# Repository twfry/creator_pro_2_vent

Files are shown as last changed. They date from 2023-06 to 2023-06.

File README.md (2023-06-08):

# Creator Pro 2 Vent Attachment for Hood

## Description

An adapter to easily attach a vent hose to the back of the Creator Pro 2's existing hood and fully vent all fumes. Does not require modifying the hood or the Creator Pro 2 in any manner.

Designed in OpenSCAD and uses the Round Anything library to design it entirely with smooth edges. The code for the adapter is located on GitHub at: https://github.com/twfry/creator_pro_2_vent

After connecting the adapter to the back of the Creator Pro 2's hood, use the following to ensure all fumes are fully vented:

1. Cover all of the openings around the enclosure with masking or duct tape
2. Use an inline vent fan to suck air through the vent opening and attached hoses.

By reducing the number of openings for air to escape from the enclosure with tape and using a powerful enough vent fan all air will be drawn into the Creator Pro 2 through any remaining opening by the air being drawn into the vent by the fan. I used a basic 4 inch inline vent fan for this (AC Infinity RAXIAL S4 with 106 CFM, $29 off amazon) and found this creates enough air flow to keep the room fully fume free, or at least free enough that I no longer noticed any remaining fumes. That said 100 CFM is likely the lowest airflow that will work and a larger fan will work better, I do plan to upgrade to a 6 inch fan with more air flow in a bit.

Parts for both 4 inch and 3 inch hoses are uploaded. Additional sizes can easily be generated by adjusting the outer diameter parameter in the linked OpenSCAD code.

## Printing

Printing

Parts should be printed as oriented in the stl files and shown in the preview images. 

The adaptor is split into two separate parts for printing:

* `vent_right.scad` - Right side part which is the same size regardless of the vent hose size. 
* `vent_left.scad` - Left side part which has different sizes for different vent hoses. Included are parts for 4 inch and 3 inch vent hoses. Additional sizes can be regenerated by adjusting a parameter in the OpenSCAD code linked below.

The left side part can be printed with no supports by orienting it face down. 

The right side part needs supports only under the flat bottom of the vent, which are a few millimeters from the bed. The rest of the vent is angled and does not require supports. I found any support in FlashPrint worked fine. The rest of the part uses angles to prevent the need for supports anywhere else. 

## Assembly

After printing the two parts are joined together and then attached to the opening at the back of the Creator Pro 2's hood. 

The left and right parts are joined together using two M3 sized nuts/bolts. The nut opening on the part is hex shaped to fit the nut. It helps to first press the nut into the right side part first so that is holds in place while screwing the bolt to join the parts together. There is an insert which both aligns the parts and ensures no fumes escape through the joint. 

## Design

The adapter was designed in OpenSCAD which allows for generating new parts with new dimensions by simply adjusting individual parameters. For example, the diameter of the pipe attachment can easily be changed from 3 inches, 4 inches, 6 inches, etc. by modifying one parameter and the parts will be fully regenerated for the new size.

The OpenSCAD code is published here so the adaptor can be adjusted if needed: https://github.com/twfry/creator_pro_2_vent

## OpenSCAD Files

* `vent_right.scad` - The right side part to print
* `vent_left.scad` - The left side part to print
* `vent_assembly.scad` - Shows the two parts next to each other, used to verify alignment after changes. 
* `vent.scad` - Utility modules to buils the parts
* `vent.parameters` - Utility modules to buils the parts

## Print Files

The following are pre-generated files for printing with a high number of facets for very smooth edges. 

* `Output/vent_right.stl` - The right side part to print
* `Output/vent_left_3_inch.stl` - The left side part to print for a 3 inch vent hose
* `Output/vent_left_4_inch.stl` - The left side part to print for a 4 inch vent hose

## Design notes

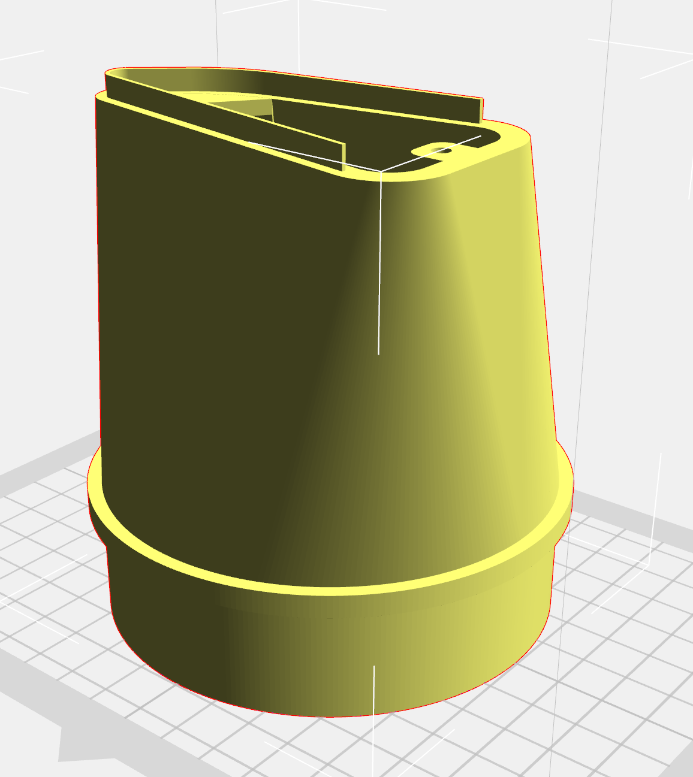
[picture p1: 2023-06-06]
images/vent_left_4_inch.png

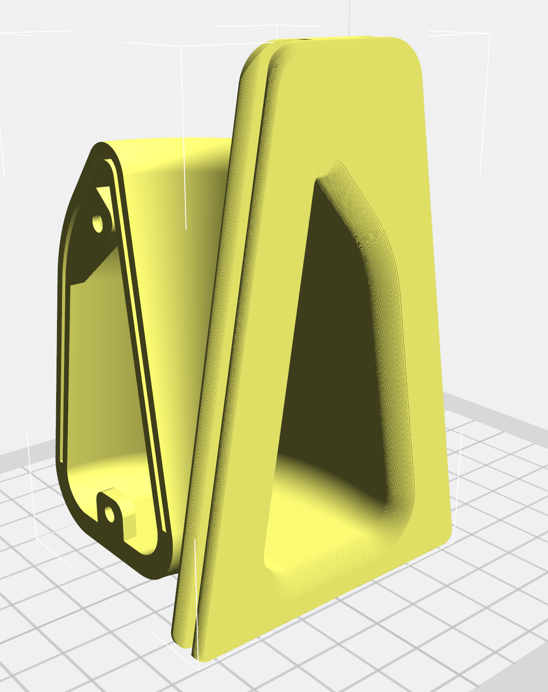
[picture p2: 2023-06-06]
images/vent_right.png

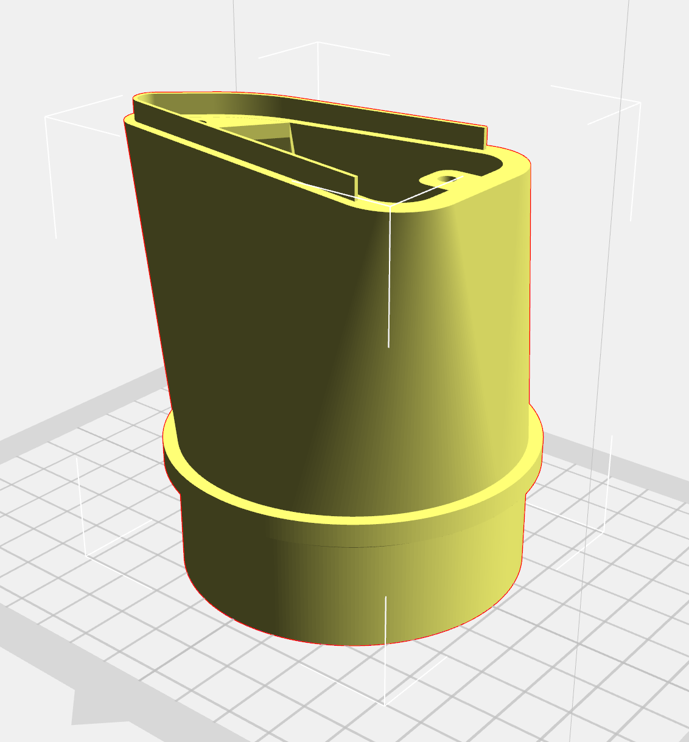
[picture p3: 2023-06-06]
images/vent_left_3_inch.png

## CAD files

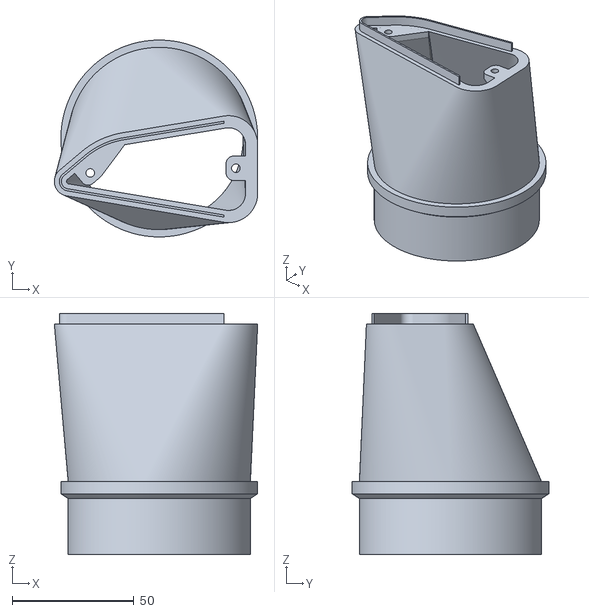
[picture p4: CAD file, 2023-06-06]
Output/vent_left_3_inch.stl
83.7 x 81.0 x 99.2

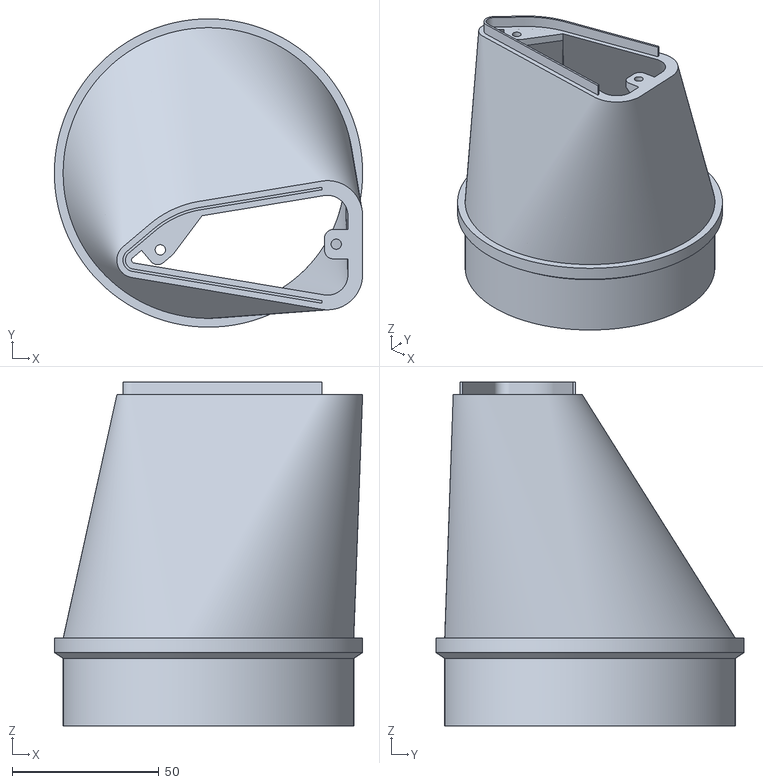
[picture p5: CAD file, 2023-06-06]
Output/vent_left_4_inch.stl
105.0 x 105.0 x 117.2

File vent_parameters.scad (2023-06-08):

// *************************************************************
//
// Vent parameters
//
// Most common to adjust are loacted at the top of the file
//
// *************************************************************



// Determines the Outer Diameter of the hose attachment 
hose_attachment_od                          = 99;           // Use for 4 inch hose
//hose_attachment_od                          = 75;           // Use for 3 inch hose


// Precision of rendering, final rendering values do take a bit but look nice

// Final rendering values
/*
$fa                                         = 1;
$fs                                         = 0.2;
fnn                                         = 30;       // Value used by RoundAnything library
radiusExtrudefn                             = 40;       // Value used by RoundAnything library
*/

// Edit rendering values
$fa                                         = 3;
$fs                                         = 1;
fnn                                         = 12;       // Value used by RoundAnything library
radiusExtrudefn                             = 10;       // Value used by RoundAnything library


// Controls the opening hole into the Creator Pro 2
hood_hole_bottom_width                      = 54.7 - 5;
hood_hole_top_width                         = 15.5 - 3;
hood_hole_height                            = 100  + 5;
hood_wall_width                             = 2.75 + 0.5;

// Controls the insert into the Creator Pro 2's hood
hood_cover_length_over_hood                 = 10;
hood_cover_width_around_hood                = 3;
hood_cover_outside_radius_top               = 8;
hood_cover_outside_radius_bottom            = 3;
hood_cover_front_radius                     = hood_cover_width_around_hood / 2;
hood_cover_back_radius                      = hood_cover_width_around_hood / 2;
hood_cover_total_width                      = hood_cover_width_around_hood * 2 + hood_wall_width;
hood_cover_x_dist                           = ( hood_hole_bottom_width/2 + hood_cover_length_over_hood ) -
                                              ( hood_hole_top_width/2 + hood_cover_length_over_hood ); 
hood_cover_y_dist                           = hood_hole_height;
hood_cover_interior_width                   = 5;
hood_cover_interior_radius_top              = 1;
hood_cover_interior_radius_middle           = 30;
hood_cover_interior_radius_bottom           = 7;
hood_cover_interior_dist_from_top           = 25;
hood_cover_interior_dist_from_bottom        = 9;

// Controls the curved segment between the Creator Pro 2 hood attachment and the hose attachment
hood_corner_curve                           = 10;
hood_corner_width                           = 5;
hood_corner_angle                           = 90;

// Controls the hose attachment pipe (the OD size of the pipe is at the top)
hose_attachment_width                       = 3;
hose_attachment_length                      = 25;
hose_attachment_stop_length                 = 5;
hose_attachment_stop_protrusion             = 3;
hose_attachment_stop_protrusion_print_shelf = 0.66;
hose_attachment_location_y                  = hose_attachment_od/2 + hose_attachment_stop_protrusion + 5;
hose_attachment_location_z                  = hose_attachment_od/2 + hose_attachment_stop_protrusion + hood_cover_interior_dist_from_bottom - hood_cover_interior_width;
hose_attachment_location_x_ratio            = 1.5;
hose_attachment_location_x                  = hose_attachment_location_x_ratio * -hose_attachment_location_y - hood_hole_bottom_width/2;

// Controls the bolt connector used to join the two parts
bolt_connector_height                       = 8;
bolt_connector_width                        = 10;
bolt_connector_depth                        = 6;
bolt_connector_radius                       = 3;
bolt_connector_bolt_dia                     = 3.5;
bolt_connector_bolt_head_dia                = 6.3;
bolt_connector_capture_nut_depth            = 1.5;

// Controls the insert wedge between the two parts
interface_insert_width                      = 1;
interface_insert_margin                     = 0.15;
interface_insert_depth                      = 4.5;

// Controls the clip to join the two parts (not used in favor of the bolt connector above)
interface_clip_width                        = 8;
interface_clip_depth                        = 1;
interface_clip_pipe_section_angle_to_connect= 60;

// Utility parameters
epsilon                                     = 0.01;
//$fn                                         = fnn;
cube_subtract_size                          = 500;



// The hood cover exterior radiiPoints
hood_cover_outside_radiiPoints = [
    [ -hood_hole_bottom_width/2 - hood_cover_length_over_hood, 0,                hood_cover_outside_radius_bottom ],
    [ -hood_hole_top_width/2    - hood_cover_length_over_hood, hood_hole_height, hood_cover_outside_radius_top ],
    [  hood_hole_top_width/2    + hood_cover_length_over_hood, hood_hole_height, hood_cover_outside_radius_top ],
    [  hood_hole_bottom_width/2 + hood_cover_length_over_hood, 0,                hood_cover_outside_radius_bottom ],
];

// The hood cover interior hole radiiPoints
//    Pre-calculate the vertical and horizontal points based on the slope from the top to bottom
//    to maintain a constant width while maximizing the opening
inside_bottom_vert          = hood_cover_interior_dist_from_bottom;
inside_bottom_horz          = hood_hole_top_width/2 + hood_cover_x_dist * ((hood_hole_height-inside_bottom_vert)/hood_hole_height) - hood_cover_interior_width;
inside_top_left_vert        = hood_hole_height - hood_cover_interior_dist_from_top;
inside_top_left_horz        = hood_hole_top_width/2 + hood_cover_x_dist * ((hood_hole_height-inside_top_left_vert)/hood_hole_height) - hood_cover_interior_width;
inside_top_right_vert       = hood_hole_height - hood_cover_interior_dist_from_top - inside_top_left_horz * 2 * 1.5;
inside_top_right_horz       = hood_hole_top_width/2 + hood_cover_x_dist * ((hood_hole_height-inside_top_right_vert)/hood_hole_height) - hood_cover_interior_width;
hood_cover_inside_radiiPoints = [
    [ -inside_bottom_horz,      0,                                                hood_cover_interior_radius_bottom ],
    [ -inside_top_left_horz,    inside_top_left_vert-hood_cover_interior_width,   hood_cover_interior_radius_top ],
    [  inside_top_right_horz,   inside_top_right_vert-hood_cover_interior_width,  hood_cover_interior_radius_middle ],
    [  inside_bottom_horz,      0,                                                hood_cover_interior_radius_bottom ],
];

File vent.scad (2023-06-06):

// *************************************************************
//
// Modules to build up the vent components
//
// This file instantiates the entire vent as a single object, use 
//   vent_left.scad and vent_right.scad for the individual parts
//
// *************************************************************


include <libs/Round-Anything/polyround.scad>
include <libs/roundedcube_simple.scad>

include <vent_parameters.scad>




// The hood attachment which connects the vent to the Creator Pro 2 hood
module hood_attachment() {

    difference() {

        // Base shape
        // translate( [ 0, hood_cover_total_width / 2 - epsilon/2, 0 ] )
        translate( [ 0, hood_cover_total_width / 2, 0 ] )
            rotate( [90, 0 , 0 ] )
                extrudeWithRadius( hood_cover_total_width, 
                                   hood_cover_back_radius, 
                                   hood_cover_front_radius, radiusExtrudefn ) 
                {
                    polygon( polyRound( hood_cover_outside_radiiPoints, fnn ) );
                };

        // Cut out side slots the hood slots into (on on both sides)
        cut_lenght = hood_hole_height * 2;
        translate( [ -hood_hole_top_width/2 - hood_cover_length_over_hood - hood_cover_x_dist/2 + hood_cover_length_over_hood/2, 
                      0, hood_cover_y_dist/2 ] )
        rotate( [ 0, asin( (hood_cover_x_dist-0.14) / hood_cover_y_dist ), 0 ] )
        rotate( [ 90, 0, -90 ] )
        translate( [ 0, 0, -hood_cover_length_over_hood/2 ])
        extrudeWithRadius( hood_cover_length_over_hood, hood_cover_front_radius/2, -hood_cover_front_radius*1.5, radiusExtrudefn )
        {
            square( [ hood_wall_width, cut_lenght ], center=true );
        };

        translate( [ hood_hole_top_width/2 + hood_cover_length_over_hood + hood_cover_x_dist/2 - hood_cover_length_over_hood/2, 
                     0, hood_cover_y_dist/2 ] )
        rotate( [ 0, -asin( (hood_cover_x_dist-0.14) / hood_cover_y_dist ), 0 ] )
        rotate( [ 90, 0, 90 ] )
        translate( [ 0, 0, -hood_cover_length_over_hood/2 ])
        extrudeWithRadius( hood_cover_length_over_hood, hood_cover_front_radius/2, -hood_cover_front_radius*1.5, radiusExtrudefn )
        {
            square( [ hood_wall_width, cut_lenght ], center=true );
        };
    
        // Cut out interior hole for venting
        translate( [ 0, hood_cover_total_width / 2, hood_cover_interior_dist_from_bottom ] )
        rotate( [90, 0 , 0 ] )
        extrudeWithRadius( hood_cover_total_width + epsilon, 0, -hood_cover_front_radius*3, radiusExtrudefn ) 
        {
            polygon( polyRound( hood_cover_inside_radiiPoints, fnn ) );
        };

    };

} // module hood_attachment()

// The curved vent behind the hood attachment point and rotates the vent 90 degrees to face the hose
module hood_corner() {
  
    translate( [ -inside_bottom_horz - hood_corner_curve, hood_cover_total_width/2 - epsilon, hood_cover_interior_dist_from_bottom - hood_corner_width ] )
    rotate_extrude( angle = hood_corner_angle, convexity = 2 )
    shell2d( hood_corner_width )
    translate( [ inside_bottom_horz + hood_corner_curve, hood_corner_width, 0 ] )
    polygon( polyRound( hood_cover_inside_radiiPoints, fnn ) );

} // moduel hood_corner()

// The end of the vent that attaches to the air ducts 
module hose_attachment() {

    translate( [ hose_attachment_location_x, hose_attachment_location_y, hose_attachment_location_z ] ) 
    rotate( [ 0, -90, 0 ] ) 
    union() {

        // Build the attachment for the hose
        translate( [ 0, 0, hose_attachment_stop_length - epsilon ] ) 
        linear_extrude( hose_attachment_length ) 
        difference() {
            circle( d = hose_attachment_od );
            circle( d = hose_attachment_od - hose_attachment_width * 2 );
        }

        // Build the attachment stop
        linear_extrude( hose_attachment_stop_length ) 
        difference() {
            circle( d = hose_attachment_od + hose_attachment_stop_protrusion * 2 );
            circle( d = hose_attachment_od - hose_attachment_width * 2 );
        }

        // To improve printing add a shelf to the attachment stop ring
        translate( [ 0, 0, hose_attachment_stop_length - epsilon ] )
        rotate_extrude( angle = 360 )
        translate( [ hose_attachment_od/2 - epsilon, 0, 0 ] )
        polygon( [ 
                   [ 0, 0 ],
                   [ hose_attachment_stop_protrusion + epsilon, 0 ],
                   [ 0, hose_attachment_stop_protrusion * hose_attachment_stop_protrusion_print_shelf ],
                 ]);

    }

}


// The vent section that connects the hose attachment to the curved section
module pipe() {

    // Subtract the outer and inner shapes to build the pipe
    difference() {

        // Build the outer shape of the pipe
        hull() {

            // The outside of the pipe attachment shape
            translate( [ hose_attachment_location_x - epsilon, hose_attachment_location_y, hose_attachment_location_z ] ) 
            rotate( [ 0, -90, 0 ] ) 
            linear_extrude( epsilon ) 
            circle( d = hose_attachment_od );

            // The outside of the curve shape
            translate( [ -(hood_corner_curve + inside_bottom_horz) + epsilon, 
                        hood_cover_total_width/2 + hood_corner_curve + inside_bottom_horz, 
                        hood_cover_interior_dist_from_bottom ] )
            rotate( [ 90, 0, 90 ] ) 
            linear_extrude( epsilon ) 
            offset( hood_corner_width )
            polygon( polyRound( hood_cover_inside_radiiPoints, fnn ) );
        
        }

        // Build the inner shape of the pipe to subtract
        hull() {

            // The inside of the pipe attachment shape
            translate( [ hose_attachment_location_x - epsilon, hose_attachment_location_y, hose_attachment_location_z ] ) 
            rotate( [ 0, -90, 0 ] ) 
            linear_extrude( epsilon*2 ) 
            circle( d = hose_attachment_od - hose_attachment_width * 2  );

            // The inside of the curve shape
            translate( [ -(hood_corner_curve + inside_bottom_horz) + epsilon, 
                        hood_cover_total_width/2 + hood_corner_curve + inside_bottom_horz, 
                        hood_cover_interior_dist_from_bottom ] )
            rotate( [ 90, 0, 90 ] ) 
            linear_extrude( epsilon*2 ) 
            polygon( polyRound( hood_cover_inside_radiiPoints, fnn ) );

        }

    }

}

module bolt_connector_bottom() {

    bolt_connector_bottom_radiiPoints = [
        [ -bolt_connector_width/2,  0,                      0 ],
        [ -bolt_connector_width/2,  bolt_connector_height,  bolt_connector_radius ],
        [  bolt_connector_width/2,  bolt_connector_height,  bolt_connector_radius ],
        [  bolt_connector_width/2,  0,                      0 ],
    ];

    translate( [ -(hood_corner_curve + inside_bottom_horz - bolt_connector_depth/2), 
                 inside_bottom_horz + hood_corner_curve + hood_corner_width, 
                 hood_cover_interior_dist_from_bottom - epsilon ] )
    rotate( [ 0, 0, -90 ] )
    difference() {

        // Build the connector shape
        hull() {

            // The connector shape itself
            rotate( [ 90, 0, 0 ] )
            linear_extrude( bolt_connector_depth ) 
            polygon( polyRound( bolt_connector_bottom_radiiPoints, fnn ) );

            // A shape in front of the connector to create a shape for 3 printing without supports
            translate( [ 0, -bolt_connector_depth, 0 ] )
            rotate( [ 180, 0, 0 ] )
            linear_extrude( epsilon ) 
            polygon( polyRound( bolt_connector_bottom_radiiPoints, fnn ) );

        }

        // Subtract the nut cutouts
        // The center cutout
        translate( [ 0, 0, bolt_connector_height/2 ] )
        rotate( [ 90, 0, 0 ] )
        cylinder( h = 200, d = bolt_connector_bolt_dia, center = true );

        // The bolt nut cutout
        translate( [ 0, -bolt_connector_capture_nut_depth/2 + epsilon, bolt_connector_height/2 ] )
        rotate( [ 90, 90, 0 ] )
        cylinder( h = bolt_connector_capture_nut_depth, d = bolt_connector_bolt_head_dia, center = true, $fn = 6 );

        // A cutout into the left part printing element for the head
        translate( [ 0, -bolt_connector_depth - bolt_connector_height/2 + bolt_connector_bolt_dia/2, bolt_connector_height/2 ] )
        rotate( [ 90, 0, 0 ] )
        cylinder( h = bolt_connector_height, d = bolt_connector_bolt_head_dia );
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

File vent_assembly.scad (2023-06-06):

// *************************************************************
//
// Shows the two parts positioned next to each other to visualize the assembly
// 
// Use "vent_right.scad" and "vent_left.scad" to print the individual parts
//
// *************************************************************

use <vent_right.scad>
use <vent_left.scad>

vent_right();

translate( [ -20, 0, 0 ] )
vent_left();

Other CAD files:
vent_left.scad
vent_right.scad
